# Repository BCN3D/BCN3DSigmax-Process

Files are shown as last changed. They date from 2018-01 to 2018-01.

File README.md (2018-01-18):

# Process Engineering

---

## What’s hold in this repository?
In the present repository you will find all the documentation needed to assemble a BCN3D Sigmax, from the warehouse to the box. In our commitment to Open Source, we want to be transparent, not only in the design, but also in the processes involved in the BCN3D Sigmax manufacture.

Since it’s our first experience producing in an assembly line, we’ve built the structure from the ground up. In the process we have made some mistakes and faced many challenges. But day after day, we improved and deployed a solid system that is allowing us to increase month after month our production capacity in order to satisfy the growing demand.

Read the full story about the Process Engineering performed at the BCN3D facilities at the [BCN3DSigma-Process repository](https://github.com/BCN3D/BCN3DSigma-Process).

After thousands of Sigma units assembled, the process of assembling 3D printers at our facilities has been optimized and the overall quality of the process has been improved. However, it is necessary to keep on fighting and dealing with unexpected problems. In order to minimise the impact of external elements while ensuring the highest quality outcome, BCN3D operators use several guides, jigs, fixtures and technical documentation. All these files can be checked in this repository.

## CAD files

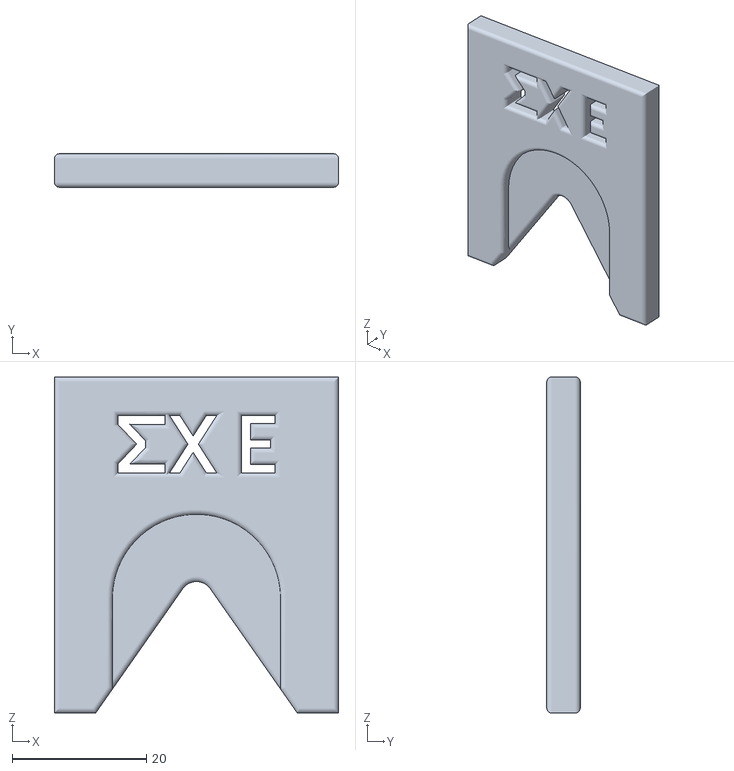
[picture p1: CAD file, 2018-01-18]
Assembly jigs/Separador Drive Gear.STL
42.3 x 5.00 x 50.0

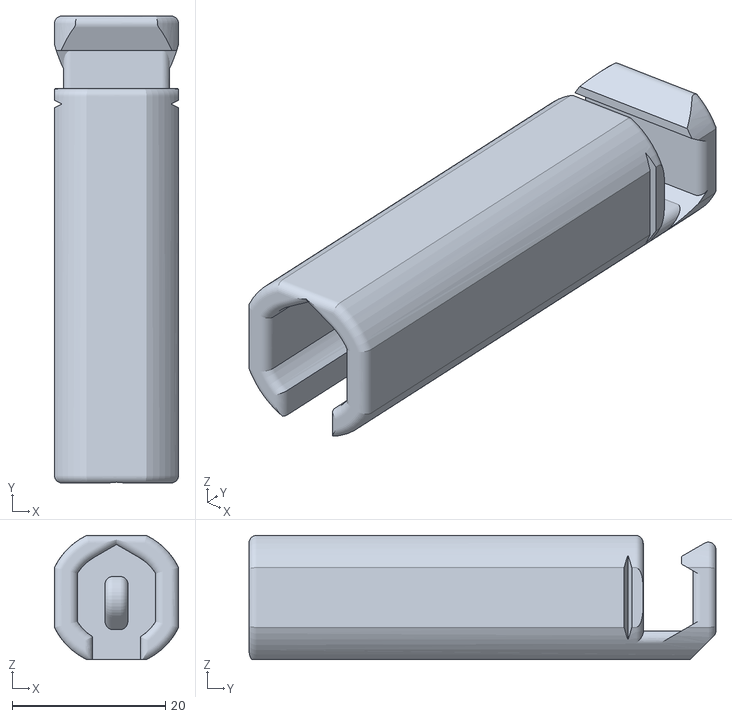
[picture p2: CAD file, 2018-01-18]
Assembly jigs/Hook tensor belt.STL
16.2 x 61.0 x 16.2

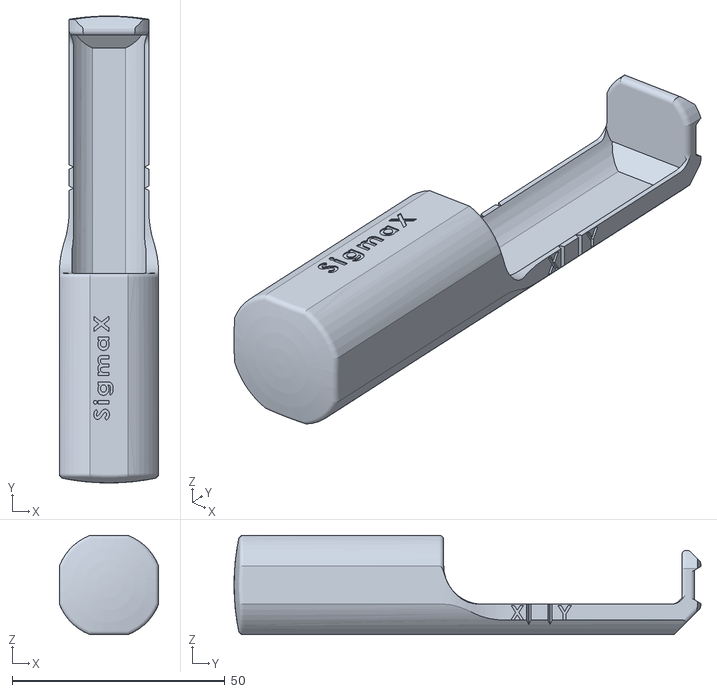
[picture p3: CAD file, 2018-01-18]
Assembly jigs/Body tensor.STL
23.3 x 109.8 x 23.3

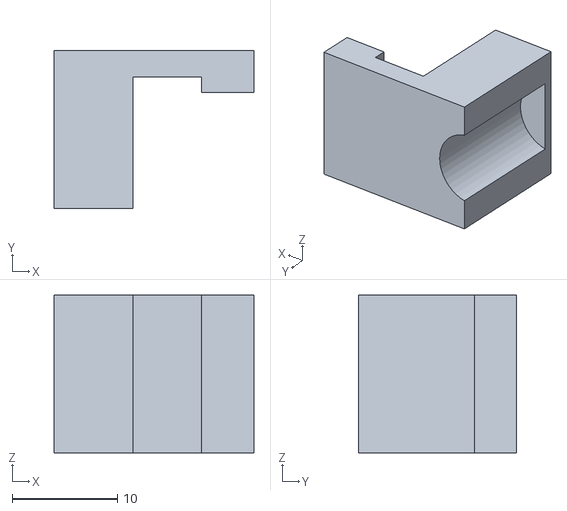
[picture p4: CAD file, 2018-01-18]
Assembly jigs/suport casquillo per talador.STL
19.0 x 15.0 x 15.0

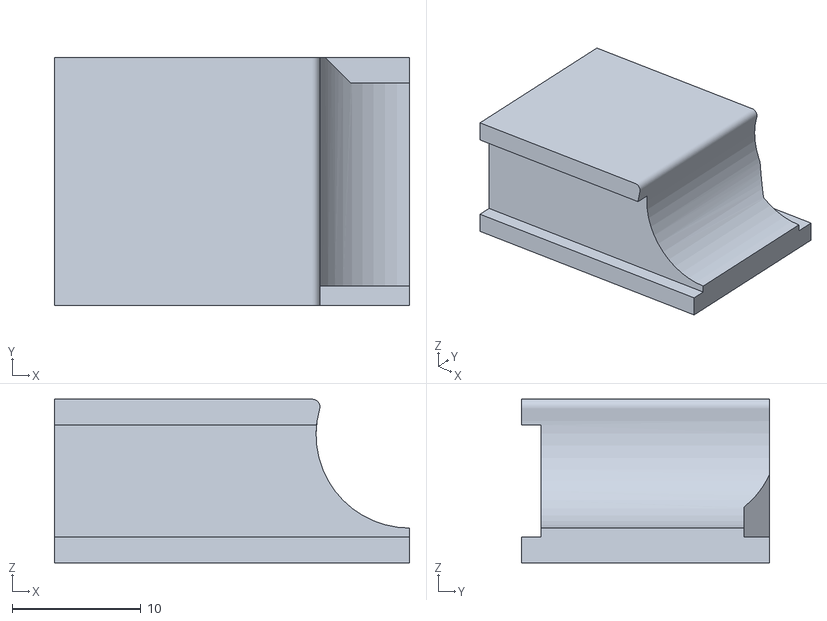
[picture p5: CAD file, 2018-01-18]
Assembly jigs/Util insert Shaft.STL
27.5 x 19.2 x 12.7

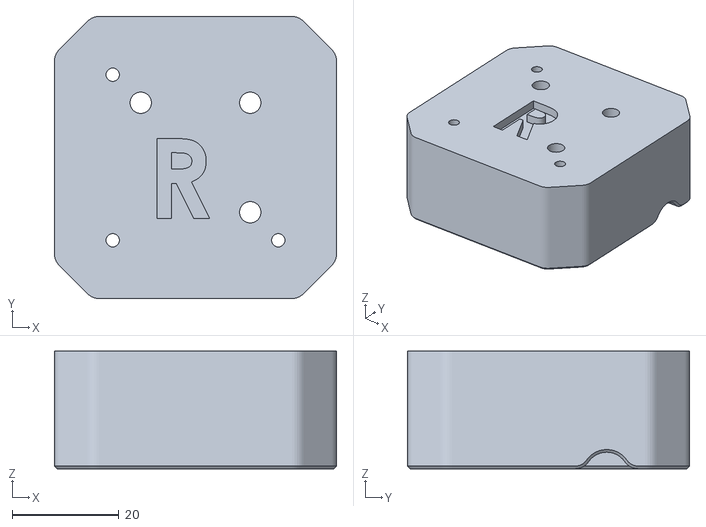
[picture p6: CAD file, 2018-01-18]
Assembly jigs/Fixtures - Right.STL
52.8 x 52.8 x 22.0

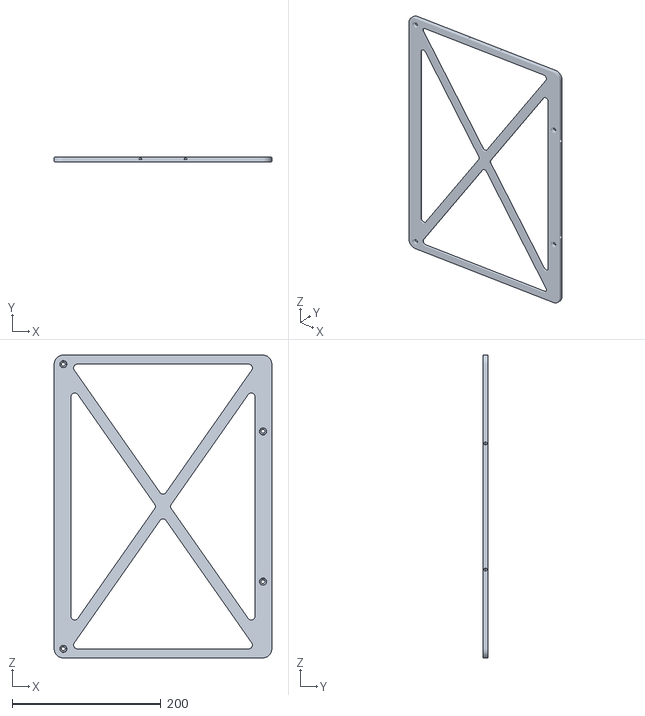
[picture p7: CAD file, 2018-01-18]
Assembly jigs/Útil per posicionar imans - PLASigmaX_v1.2.STL
293.0 x 6.50 x 407.8

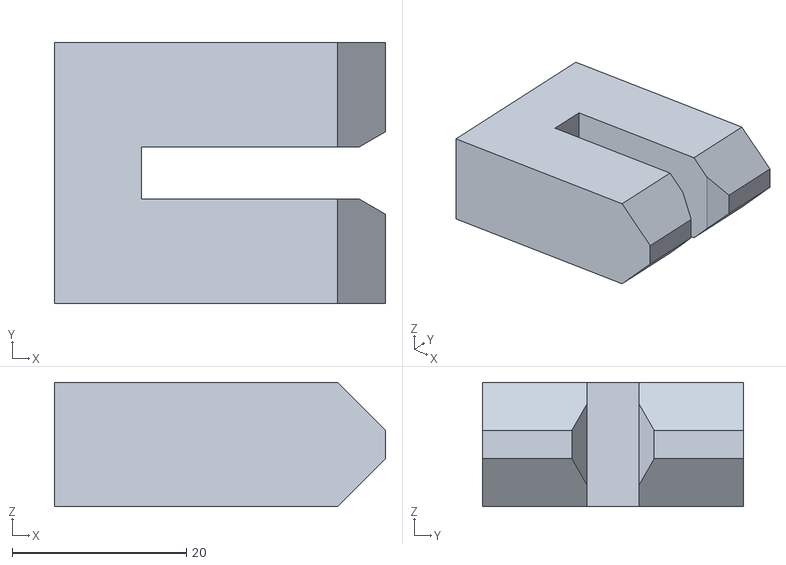
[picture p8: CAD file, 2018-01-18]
Assembly jigs/Util insert anelles.STL
38.0 x 30.0 x 14.3

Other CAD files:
Assembly jigs/Fixtures - Left.STL

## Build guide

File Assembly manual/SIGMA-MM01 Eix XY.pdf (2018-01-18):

## MANUAL DE MUNTATGE

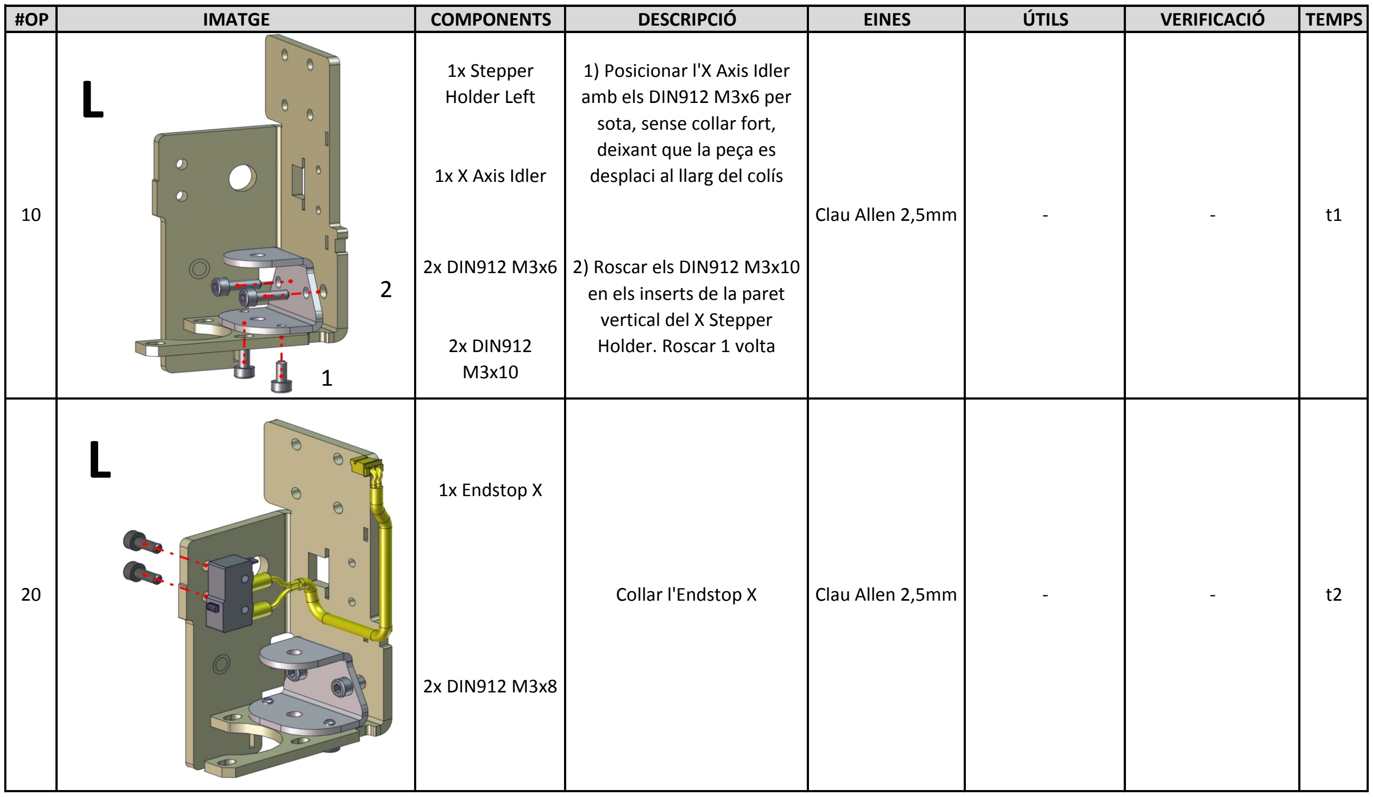
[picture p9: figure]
1x Endstop X; Clau Allen 2,5mm; 2x DIN912 M3x8; 2) Roscar els DIN912 M3x10 en els inserts de la paret vertical del X Stepper Holder. Roscar 1 volta; 1) Posicionar l'X Axis Idler amb els DIN912 M3x6 per sota, sense collar fort, deixant que la peça es desplaci al llarg del colís; Collar l'Endstop X; 2x DIN912 M3x10; 2x DIN912 M3x6; 1x X Axis Idler; 1x Stepper Holder Left L

#OP | IMATGE | COMPONENTS | DESCRIPCIÓ | EINES | ÚTILS | VERIFICACIÓ | TEMPS

CONJUNT | Eix XY
CODI DOCUMENT | SIGMA-MM01 | OPERARIS | 1 | DATA DOCUMENT | 18/01/2018
VERSIÓ DOCUMENT | v04 | TEMPS | T | CONTACTE | E. Pallarés

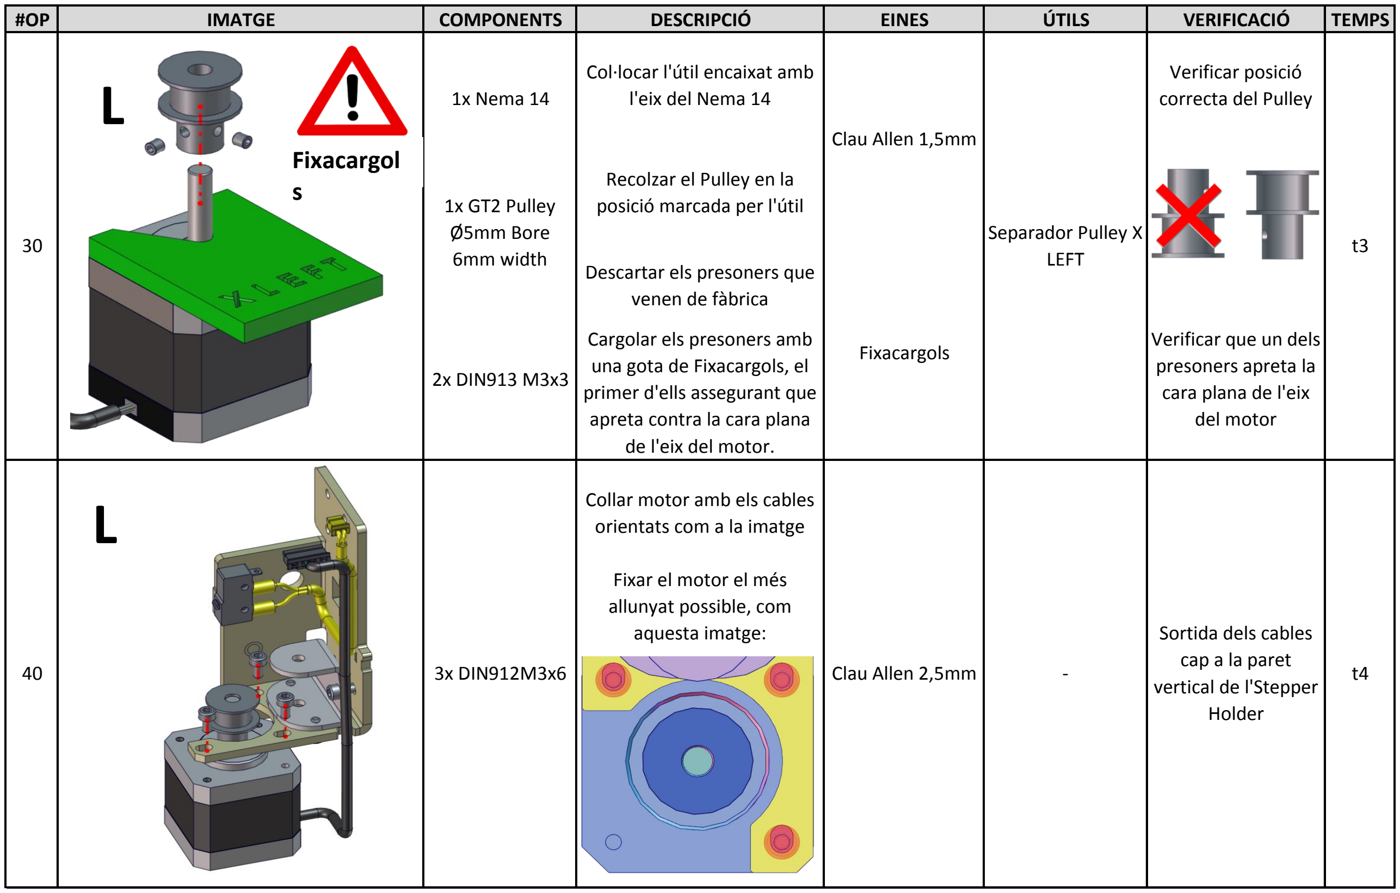
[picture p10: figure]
Cargolar els presoners amb una gota de Fixacargols, el primer d'ells assegurant que apreta contra la cara plana de l'eix del motor.; Clau Allen 1,5mm; Fixacargols; Fixar el motor el més allunyat possible, com aquesta imatge:; Col·locar l'útil encaixat amb l'eix del Nema 14; Recolzar el Pulley en la posició marcada per l'útil; Descartar els presoners que venen de fàbrica; Clau Allen 2,5mm; Sortida dels cables cap a la paret vertical de l'Stepper Holder; 3x DIN912M3x6; Verificar posició correcta del Pulley; Verificar que un dels presoners apreta la cara plana de l'eix del motor; Separador Pulley X LEFT; 1x Nema 14; 1x GT2 Pulley Ø5mm Bore 6mm width; 2x DIN913 M3x3; Collar motor amb els cables orientats com a la imatge; Fixacargol s

#OP | IMATGE | COMPONENTS | DESCRIPCIÓ | EINES | ÚTILS | VERIFICACIÓ | TEMPS

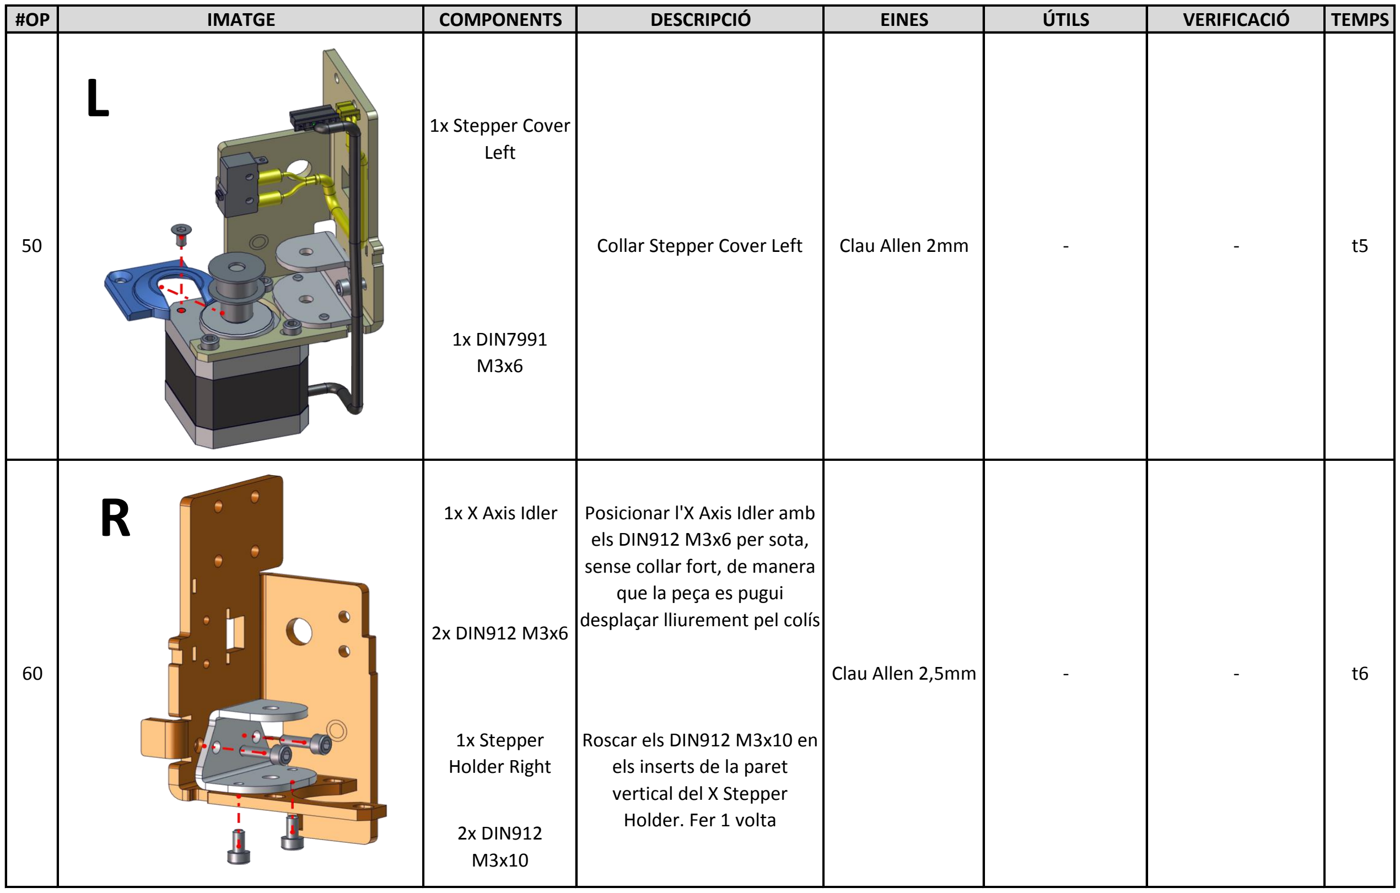
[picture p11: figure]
1x X Axis Idler; 2x DIN912 M3x6; 2x DIN912 M3x10; 1x Stepper Holder Right; Clau Allen 2mm; 1x DIN7991 M3x6; Clau Allen 2,5mm; Roscar els DIN912 M3x10 en els inserts de la paret vertical del X Stepper Holder. Fer 1 volta; Collar Stepper Cover Left; 1x Stepper Cover Left; Posicionar l'X Axis Idler amb els DIN912 M3x6 per sota, sense collar fort, de manera que la peça es pugui desplaçar lliurement pel colís

#OP | IMATGE | COMPONENTS | DESCRIPCIÓ | EINES | ÚTILS | VERIFICACIÓ | TEMPS

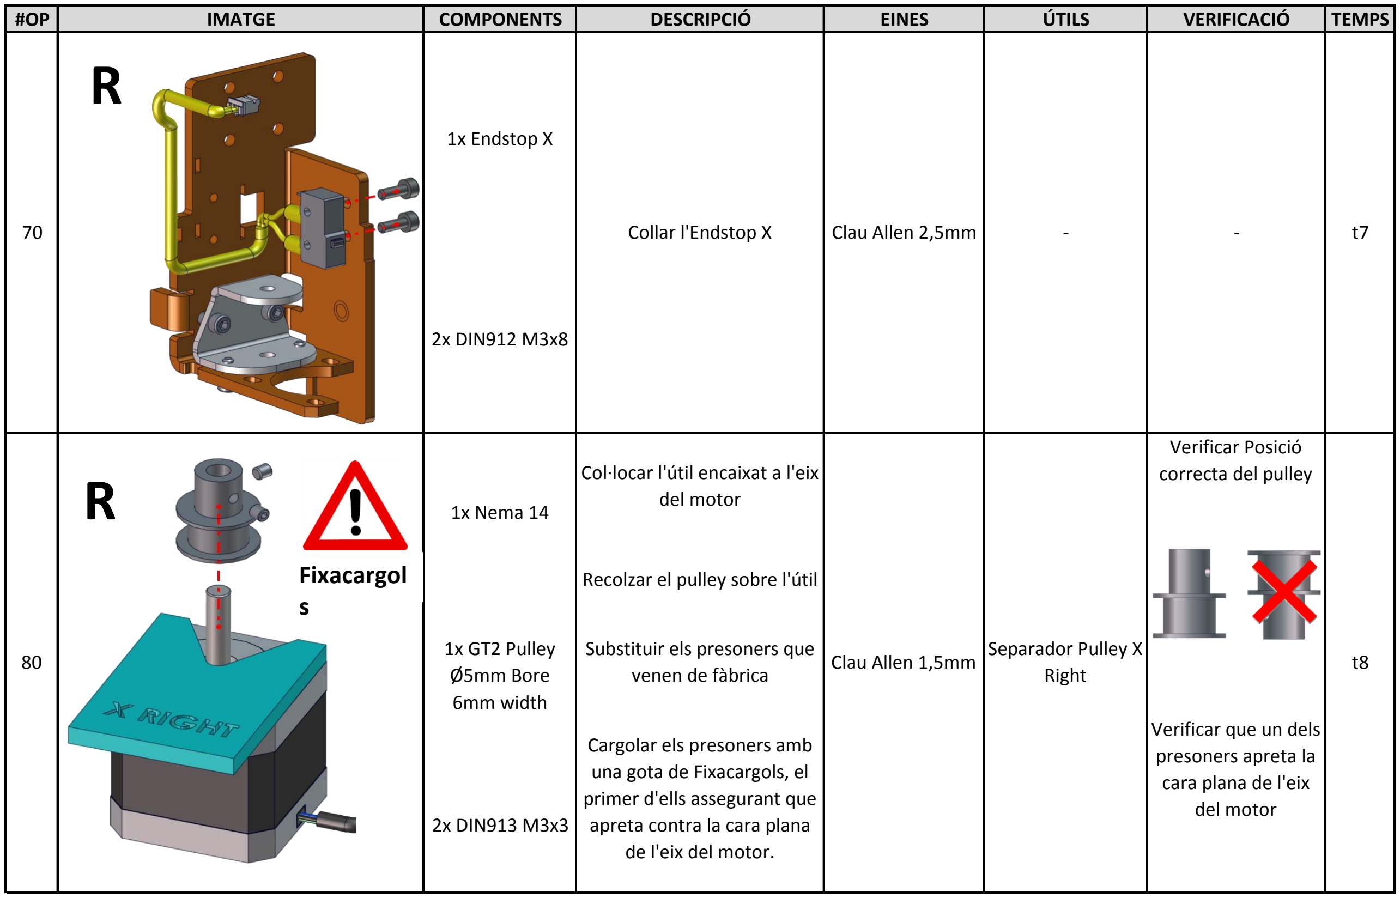
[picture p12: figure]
2x DIN912 M3x8; 1x Endstop X; Substituir els presoners que venen de fàbrica; Cargolar els presoners amb una gota de Fixacargols, el primer d'ells assegurant que apreta contra la cara plana de l'eix del motor.; Col·locar l'útil encaixat a l'eix del motor; Recolzar el pulley sobre l'útil; Verificar que un dels presoners apreta la cara plana de l'eix del motor; Clau Allen 1,5mm; Separador Pulley X; Right; 1x Nema 14; 1x GT2 Pulley Ø5mm Bore 6mm width; 2x DIN913 M3x3; Verificar Posició correcta del pulley; Fixacargol s

#OP | IMATGE | COMPONENTS | DESCRIPCIÓ | EINES | ÚTILS | VERIFICACIÓ | TEMPS

70 | Collar l'Endstop X | Clau Allen 2,5mm | - | - | t7

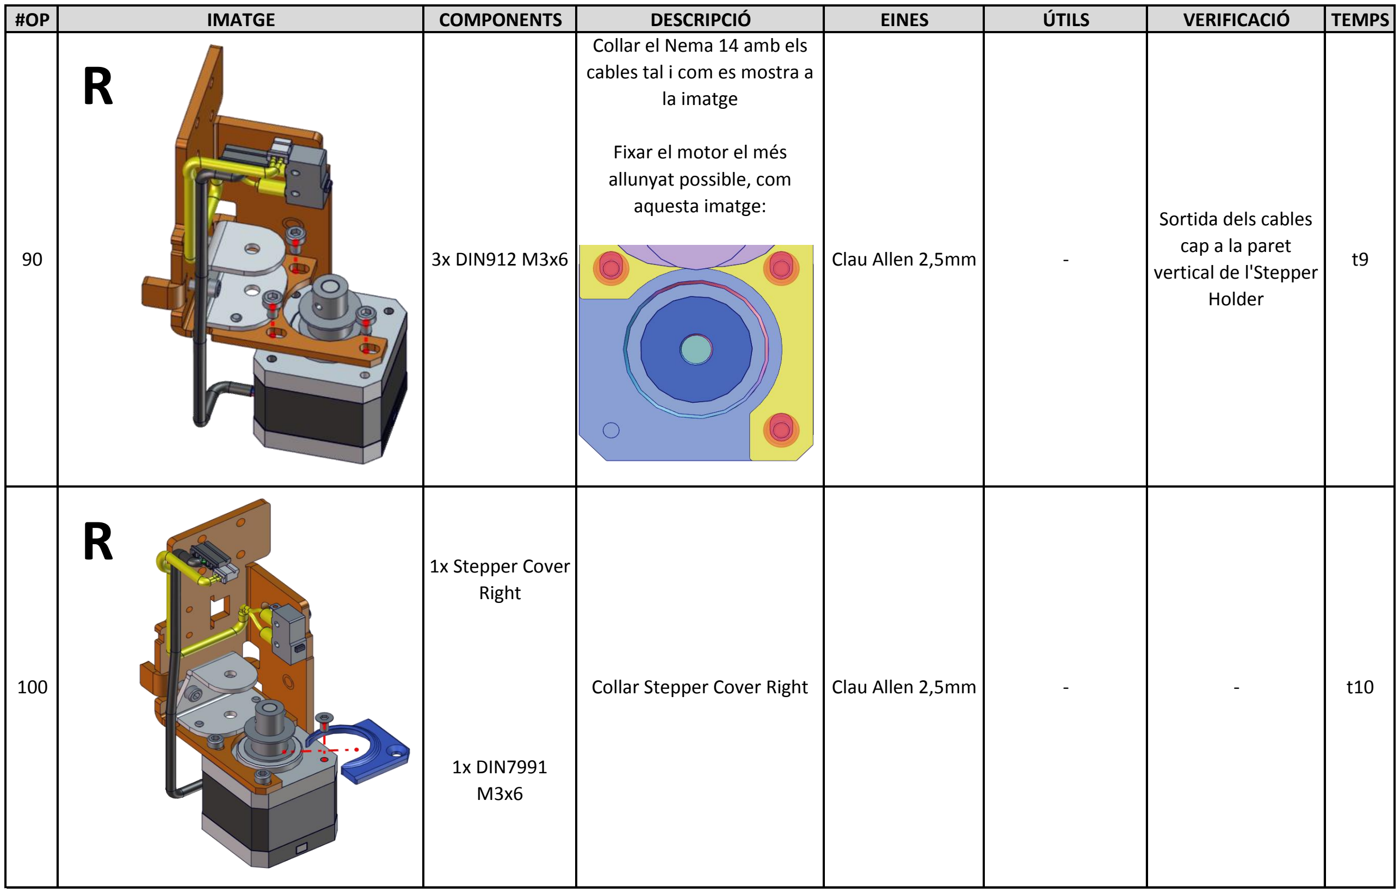
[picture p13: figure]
Fixar el motor el més allunyat possible, com aquesta imatge:; 1x DIN7991 M3x6; Sortida dels cables cap a la paret vertical de l'Stepper Holder; Collar el Nema 14 amb els cables tal i com es mostra a la imatge; 1x Stepper Cover Right; Clau Allen 2,5mm; 3x DIN912 M3x6

#OP | IMATGE | COMPONENTS | DESCRIPCIÓ | EINES | ÚTILS | VERIFICACIÓ | TEMPS

Collar Stepper Cover Right | Clau Allen 2,5mm | -

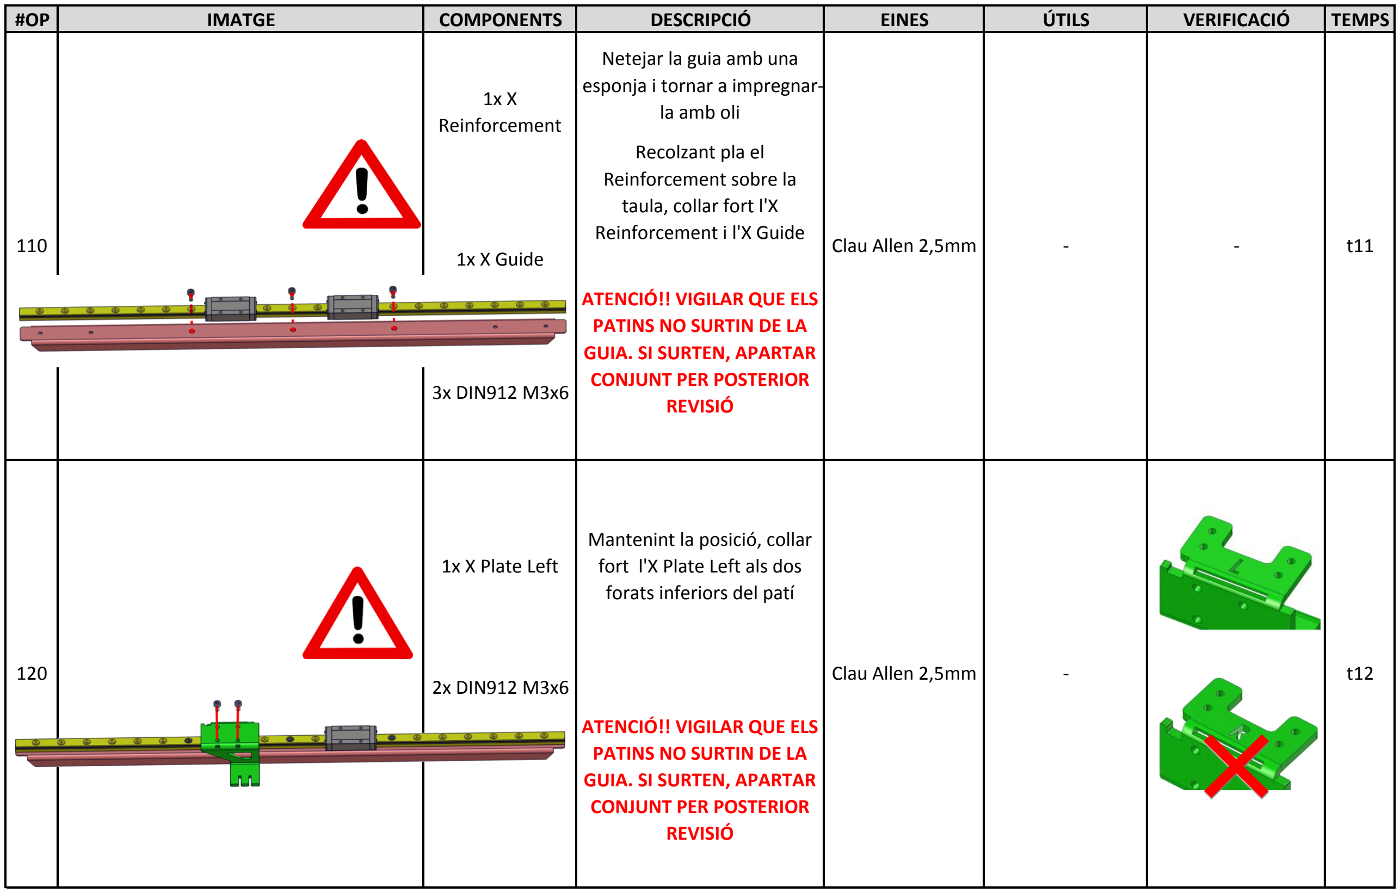
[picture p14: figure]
1x X Reinforcement; 1x X Guide; 3x DIN912 M3x6; Clau Allen 2,5mm; ATENCIÓ!! VIGILAR QUE ELS PATINS NO SURTIN DE LA GUIA. SI SURTEN, APARTAR CONJUNT PER POSTERIOR REVISIÓ; Mantenint la posició, collar fort l'X Plate Left als dos forats inferiors del patí; Recolzant pla el Reinforcement sobre la taula, collar fort l'X Reinforcement i l'X Guide; Netejar la guia amb una esponja i tornar a impregnar- la amb oli; 1x X Plate Left; 2x DIN912 M3x6

#OP | IMATGE | COMPONENTS | DESCRIPCIÓ | EINES | ÚTILS | VERIFICACIÓ | TEMPS

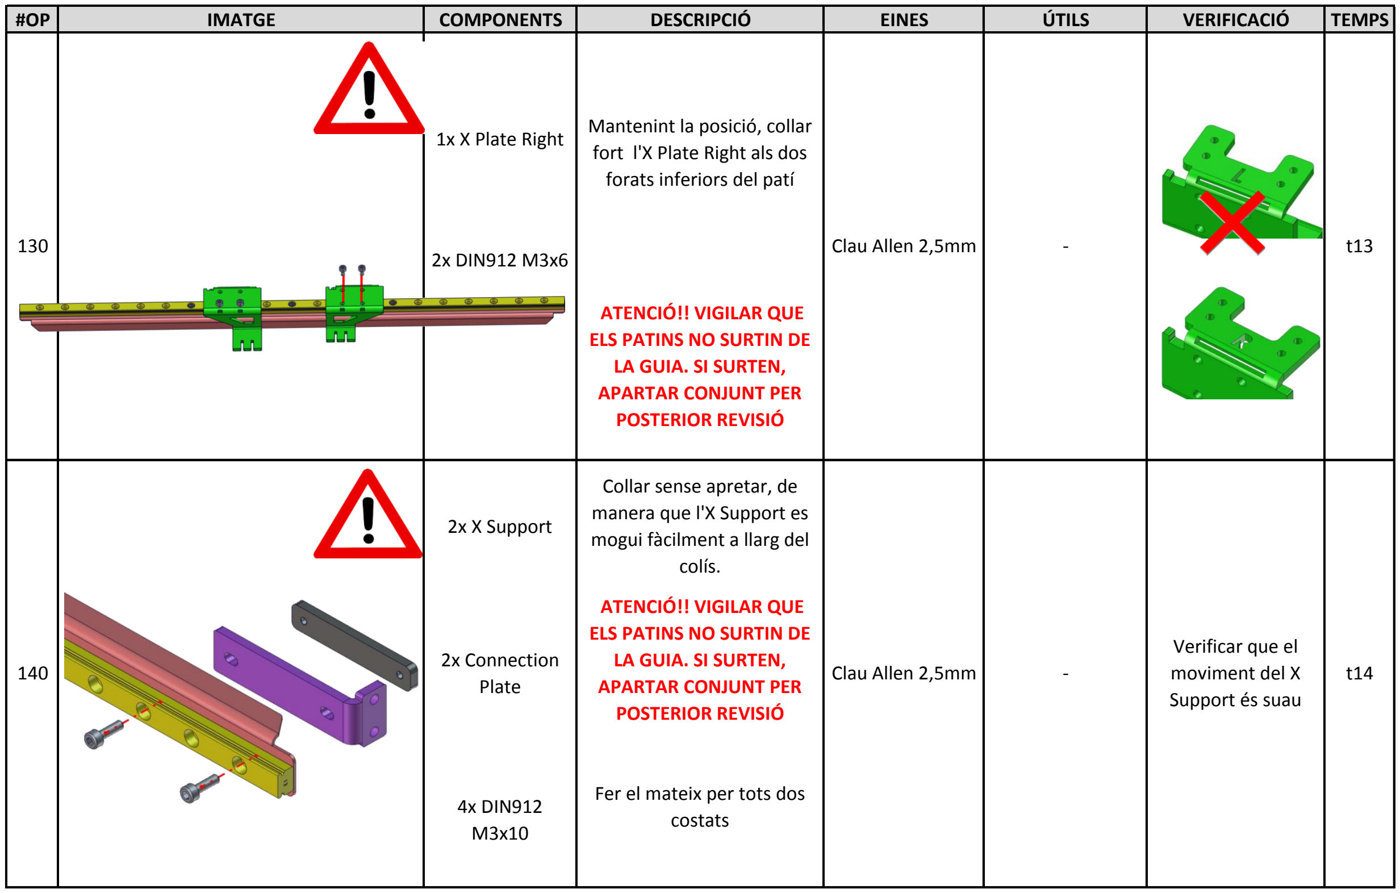
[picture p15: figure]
Fer el mateix per tots dos costats; ATENCIÓ!! VIGILAR QUE ELS PATINS NO SURTIN DE LA GUIA. SI SURTEN, APARTAR CONJUNT PER POSTERIOR REVISIÓ; Collar sense apretar, de manera que l'X Support es mogui fàcilment a llarg del colís.; 2x X Support; 2x Connection Plate; 4x DIN912 M3x10; Clau Allen 2,5mm; Mantenint la posició, collar fort l'X Plate Right als dos forats inferiors del patí; Verificar que el moviment del X Support és suau; 1x X Plate Right; 2x DIN912 M3x6

#OP | IMATGE | COMPONENTS | DESCRIPCIÓ | EINES | ÚTILS | VERIFICACIÓ | TEMPS

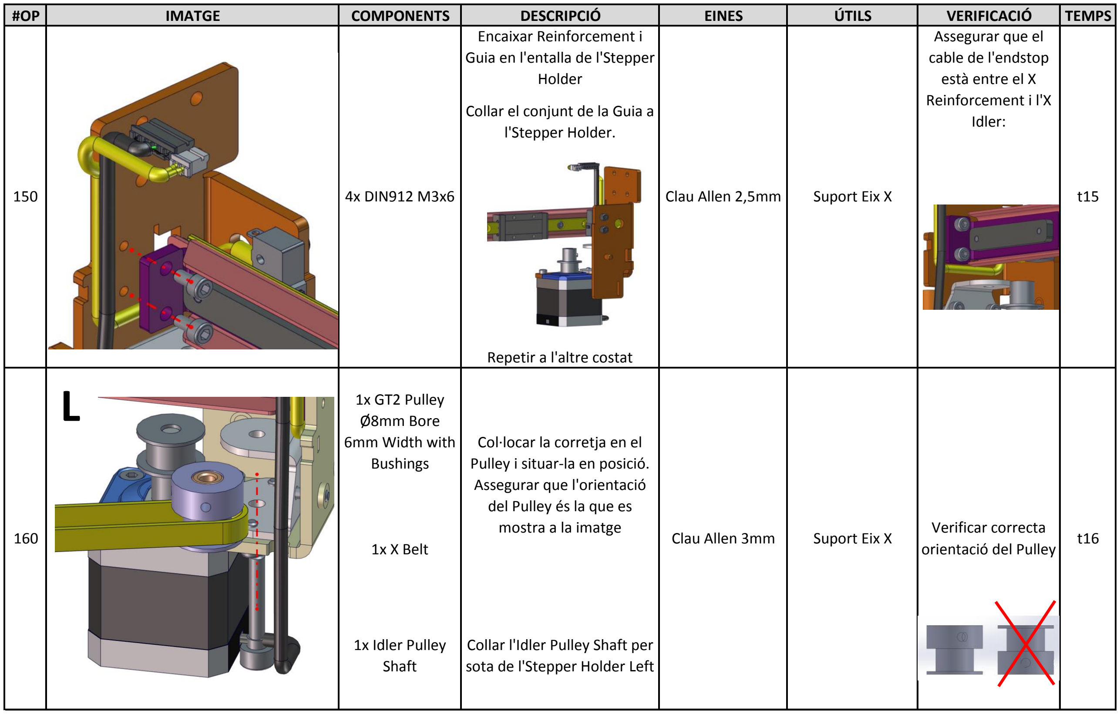
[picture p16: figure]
Repetir a l'altre costat; 1x GT2 Pulley Ø8mm Bore 6mm Width with Bushings; Clau Allen 3mm; Suport Eix X; 4x DIN912 M3x6; Assegurar que el cable de l'endstop està entre el X Reinforcement i l'X Idler:; Clau Allen 2,5mm; 1x X Belt; 1x Idler Pulley Shaft; Collar l'Idler Pulley Shaft per sota de l'Stepper Holder Left; Col·locar la corretja en el Pulley i situar-la en posició. Assegurar que l'orientació del Pulley és la que es mostra a la imatge; Encaixar Reinforcement i Guia en l'entalla de l'Stepper Holder; Collar el conjunt de la Guia a l'Stepper Holder.; Verificar correcta orientació del Pulley

#OP | IMATGE | COMPONENTS | DESCRIPCIÓ | EINES | ÚTILS | VERIFICACIÓ | TEMPS

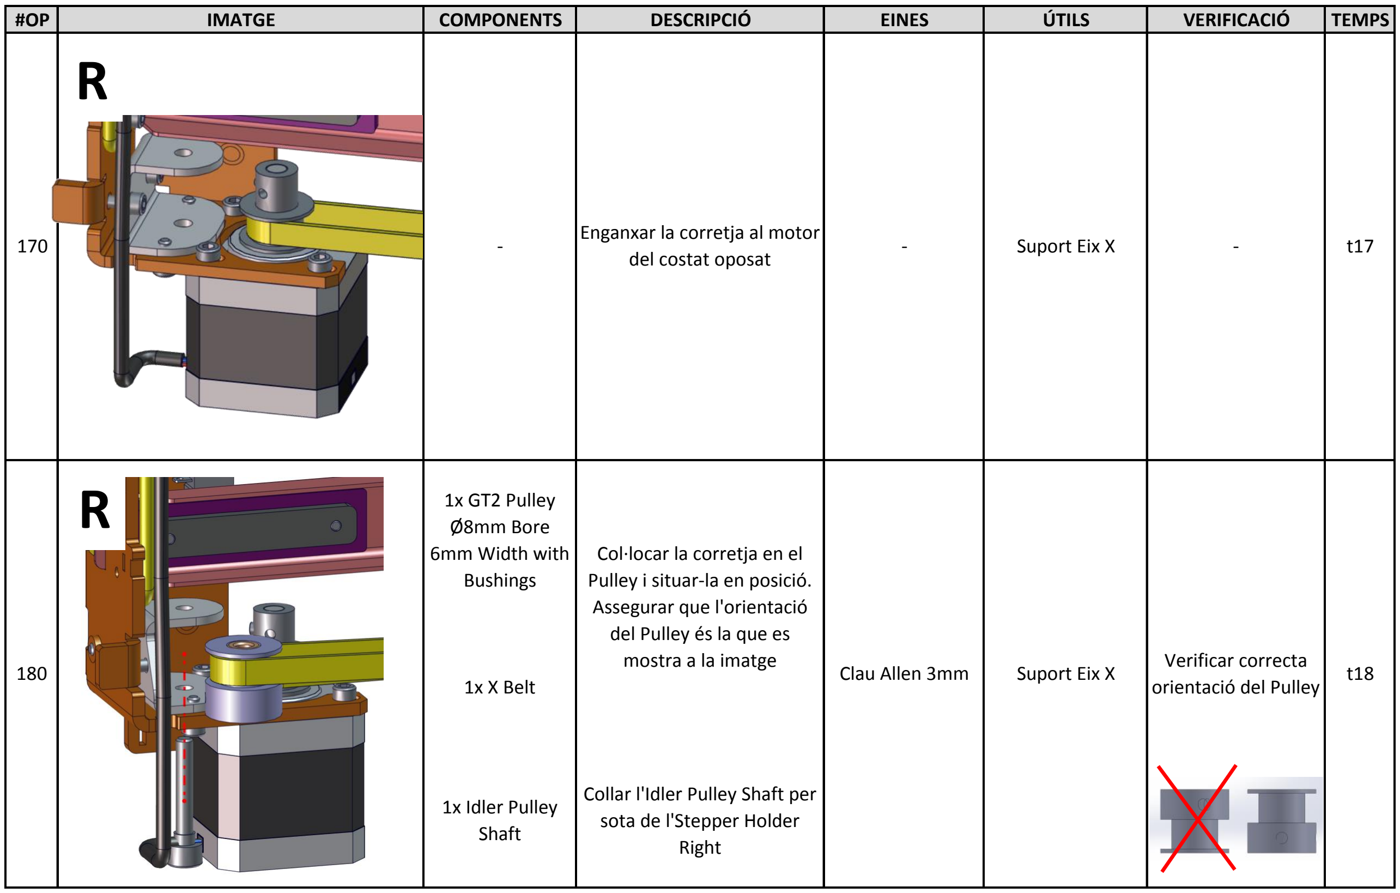
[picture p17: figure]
Enganxar la corretja al motor del costat oposat; 1x GT2 Pulley Ø8mm Bore 6mm Width with Bushings; Col·locar la corretja en el Pulley i situar-la en posició. Assegurar que l'orientació del Pulley és la que es; Verificar correcta; orientació del Pulley; t18 1x X Belt; 1x Idler Pulley Shaft; Collar l'Idler Pulley Shaft per sota de l'Stepper Holder Right; Suport Eix X

#OP | IMATGE | COMPONENTS | DESCRIPCIÓ | EINES | ÚTILS | VERIFICACIÓ | TEMPS

mostra a la imatge | Clau Allen 3mm | Suport Eix X

#OP | IMATGE | COMPONENTS | DESCRIPCIÓ | EINES | ÚTILS | VERIFICACIÓ | TEMPS

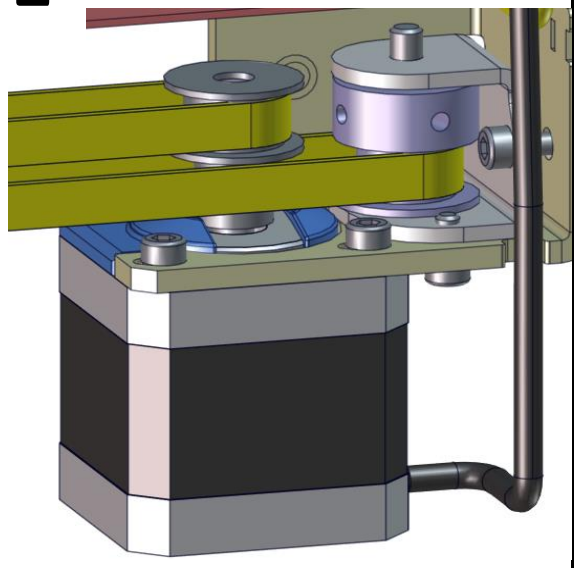
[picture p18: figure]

190 | - | - | Suport Eix X | - | t19

Enganxar la corretja al motor del costat oposat

L

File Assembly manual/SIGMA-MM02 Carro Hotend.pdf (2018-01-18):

## MANUAL DE MUNTATGE

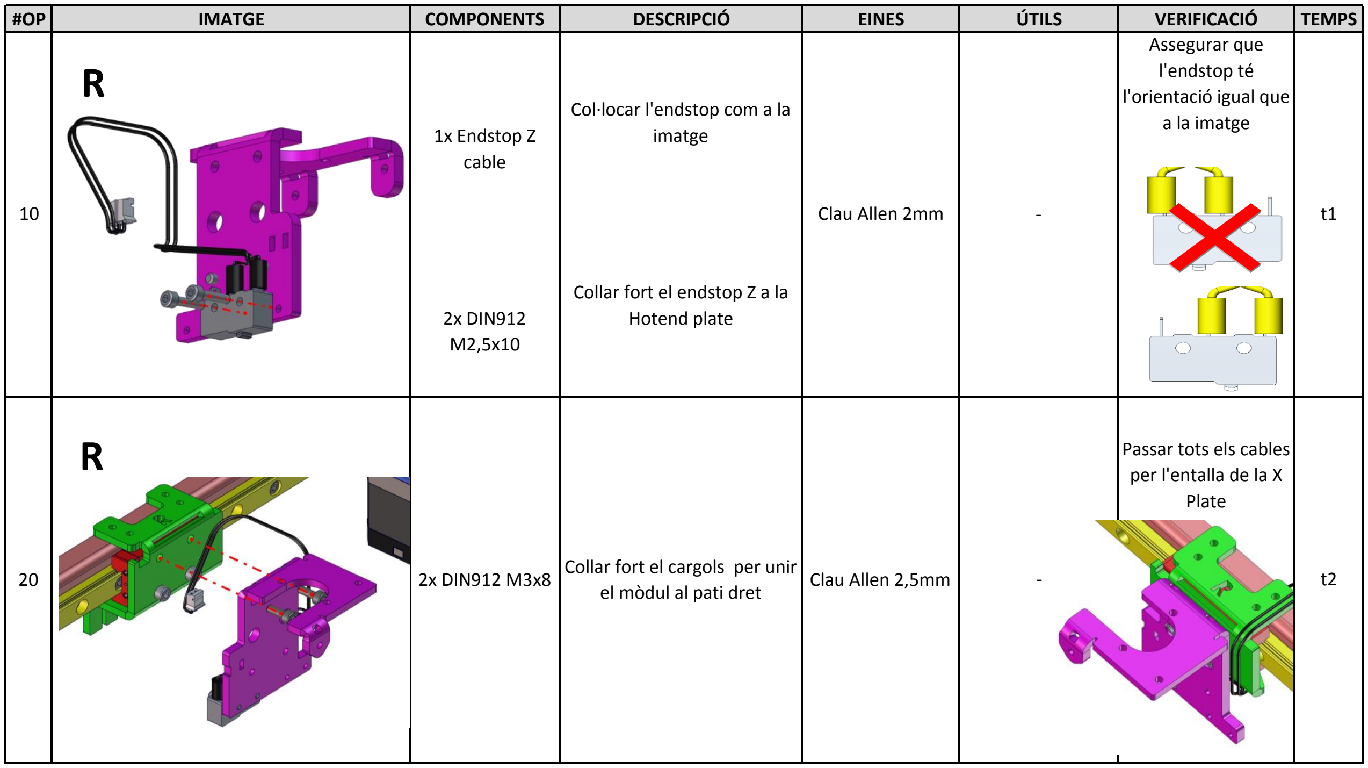
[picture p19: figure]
Collar fort el endstop Z a la; 2x DIN912; Hotend plate; Passar tots els cables per l'entalla de la X Plate; 2x DIN912 M3x8; Collar fort el cargols per unir; el mòdul al pati dret; Clau Allen 2,5mm; 1x Endstop Z cable; Col·locar l'endstop com a la imatge; Clau Allen 2mm; Assegurar que l'endstop té l'orientació igual que a la imatge

#OP | IMATGE | COMPONENTS | DESCRIPCIÓ | EINES | ÚTILS | VERIFICACIÓ | TEMPS

CONJUNT | Carro Hotend
CODI DOCUMENT | SIGMA-MM02 | OPERARIS | 1 | DATA DOCUMENT | 18/01/2018
VERSIÓ DOCUMENT | v04 | TEMPS | T | CONTACTE | E. Pallarés

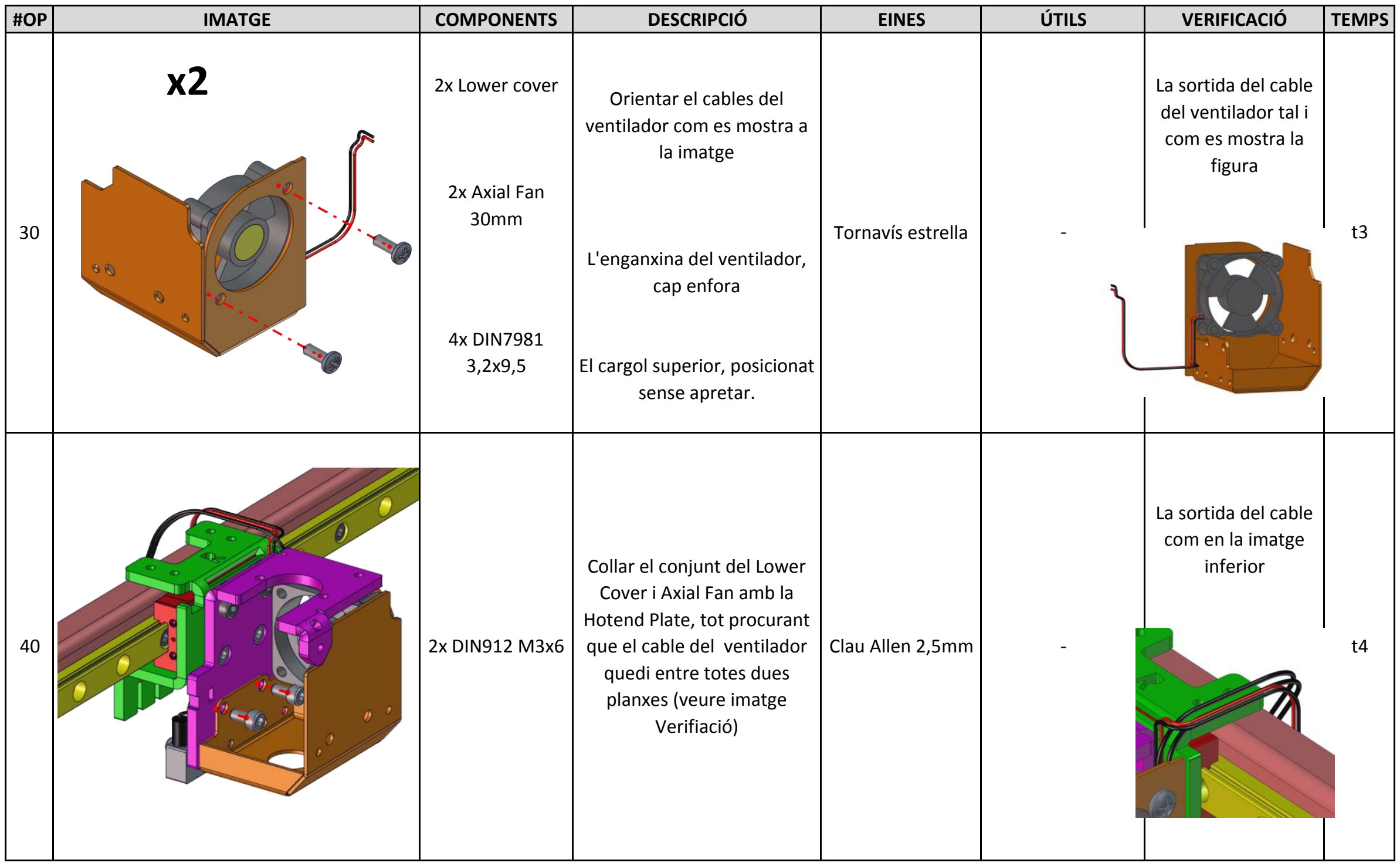
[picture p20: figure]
Orientar el cables del ventilador com es mostra a la imatge; La sortida del cable del ventilador tal i com es mostra la figura; 2x DIN912 M3x6; 2x Lower cover; 2x Axial Fan 30mm; El cargol superior, posicionat sense apretar.; 4x DIN7981 3,2x9,5; Collar el conjunt del Lower Cover i Axial Fan amb la Hotend Plate, tot procurant que el cable del ventilador quedi entre totes dues planxes (veure imatge Verifiació); Tornavís estrella; L'enganxina del ventilador, cap enfora; La sortida del cable com en la imatge inferior; Clau Allen 2,5mm

#OP | IMATGE | COMPONENTS | DESCRIPCIÓ | EINES | ÚTILS | VERIFICACIÓ | TEMPS

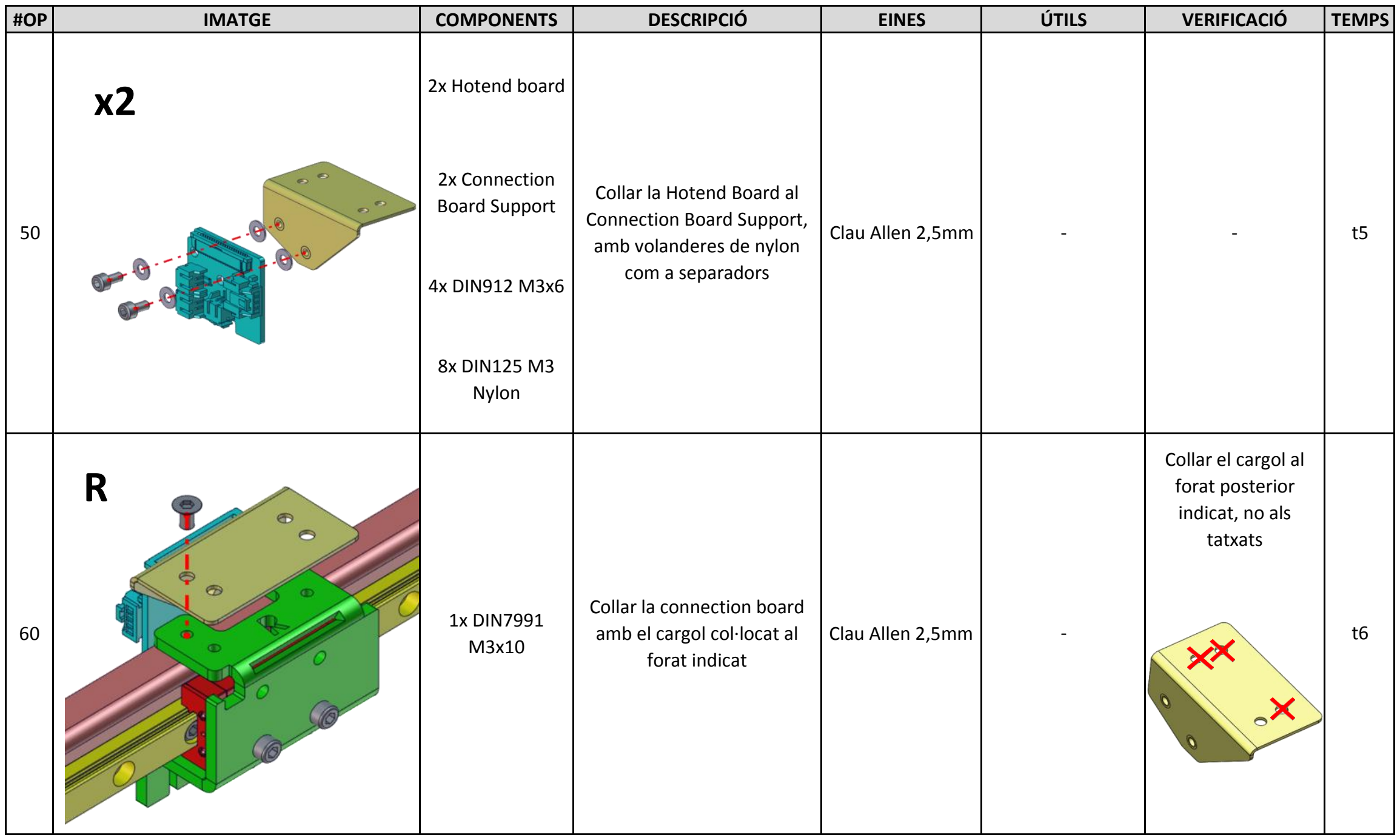
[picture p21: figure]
Clau Allen 2,5mm; Collar la connection board amb el cargol col·locat al forat indicat; 1x DIN7991 M3x10; 4x DIN912 M3x6; 8x DIN125 M3 Nylon; 2x Hotend board; 2x Connection Board Support; Collar el cargol al forat posterior indicat, no als tatxats; Collar la Hotend Board al Connection Board Support, amb volanderes de nylon com a separadors

#OP | IMATGE | COMPONENTS | DESCRIPCIÓ | EINES | ÚTILS | VERIFICACIÓ | TEMPS

#OP | IMATGE | COMPONENTS | DESCRIPCIÓ | EINES | ÚTILS | VERIFICACIÓ | TEMPS

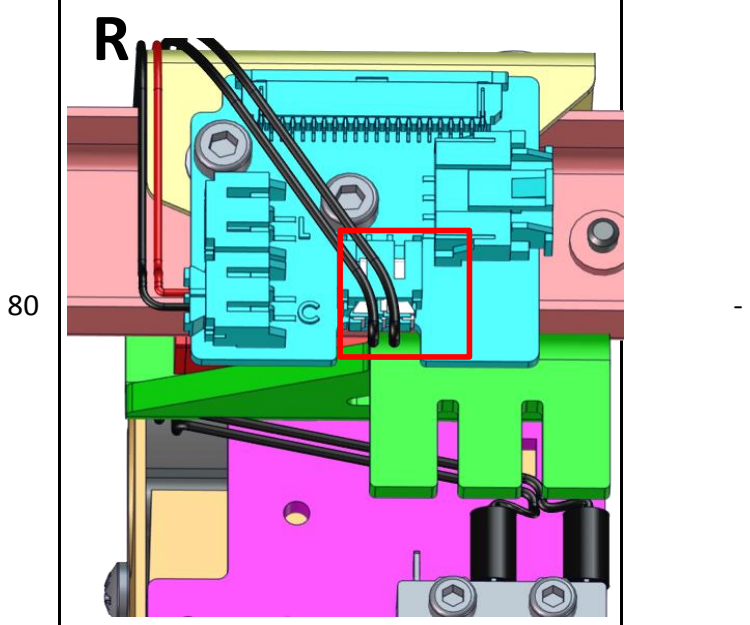
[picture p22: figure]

Connectar l'endstop al
connector indicat | -

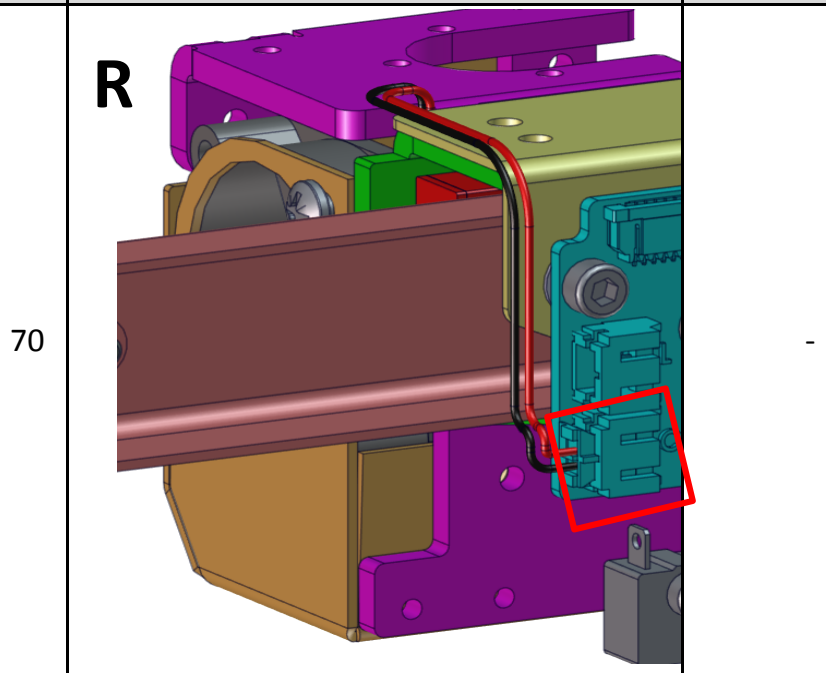
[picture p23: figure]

Trenar els cables i connectar el ventilador del hotend al connector indicat

t7

- | - | t8

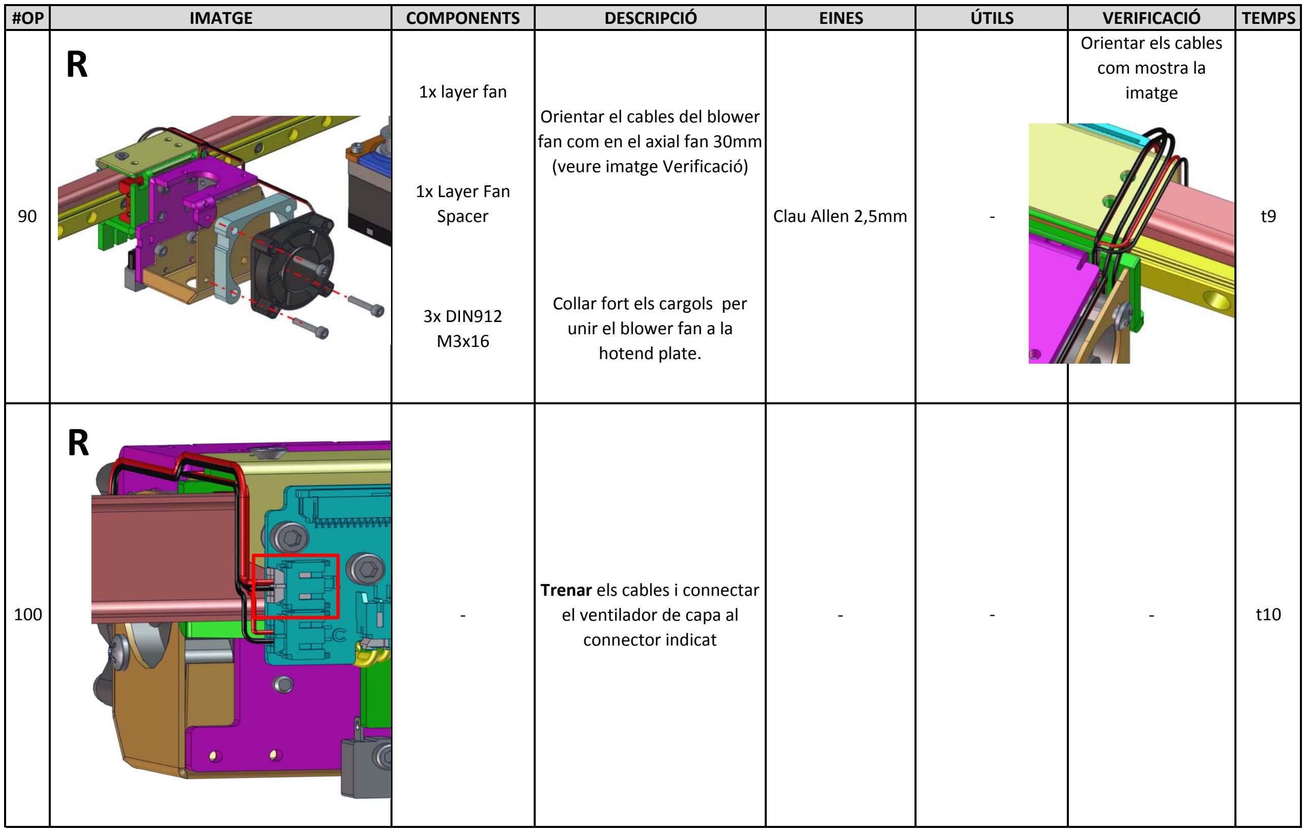
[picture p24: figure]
Trenar els cables i connectar el ventilador de capa al connector indicat; Collar fort els cargols per unir el blower fan a la hotend plate.; Orientar el cables del blower fan com en el axial fan 30mm (veure imatge Verificació); 1x layer fan; 3x DIN912 M3x16; 1x Layer Fan Spacer; Clau Allen 2,5mm; Orientar els cables com mostra la imatge

#OP | IMATGE | COMPONENTS | DESCRIPCIÓ | EINES | ÚTILS | VERIFICACIÓ | TEMPS

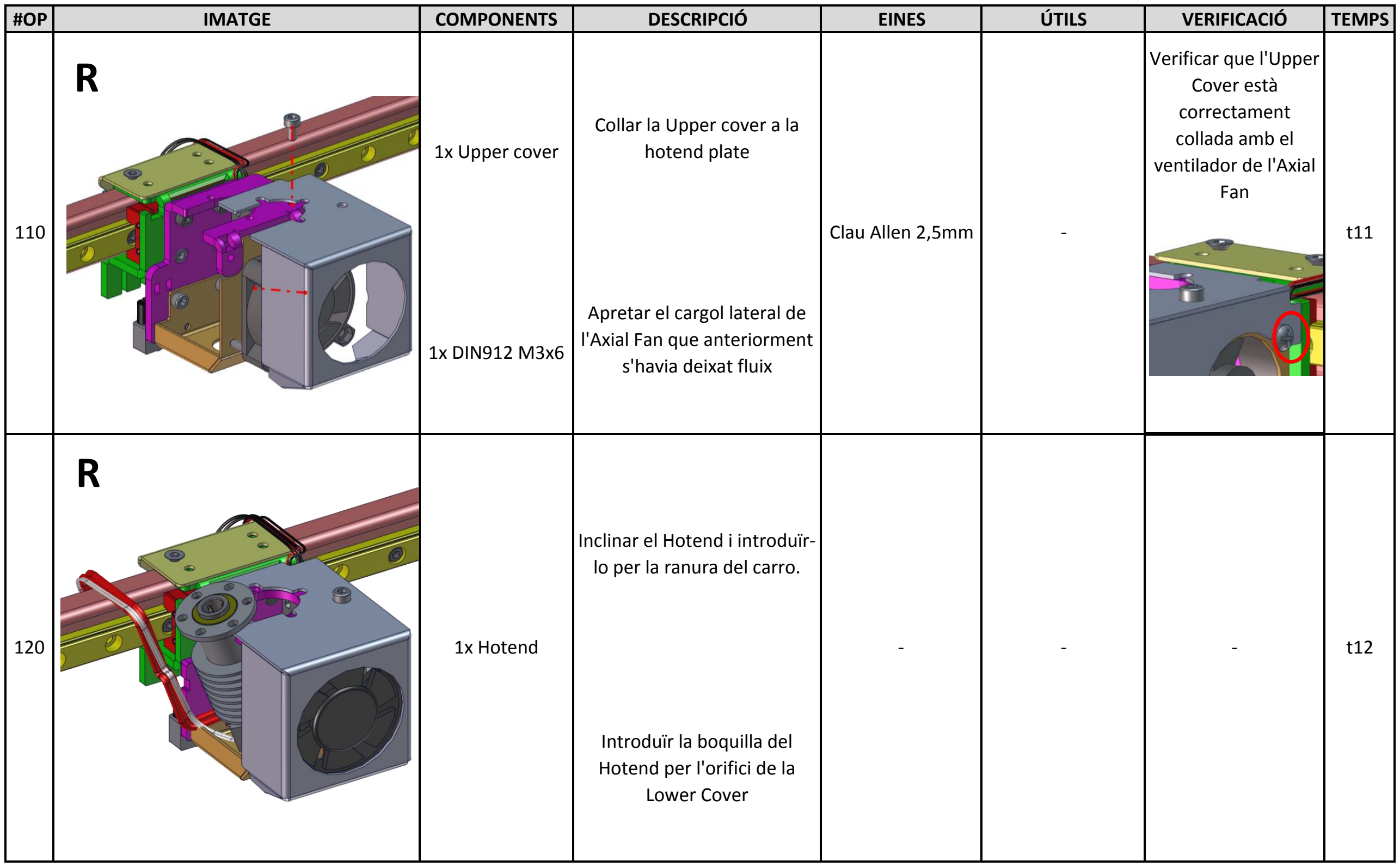
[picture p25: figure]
Inclinar el Hotend i introduïr- lo per la ranura del carro.; 1x Upper cover; Introduïr la boquilla del Hotend per l'orifici de la Lower Cover; 1x Hotend; 1x DIN912 M3x6; Clau Allen 2,5mm; Collar la Upper cover a la hotend plate; Apretar el cargol lateral de l'Axial Fan que anteriorment s'havia deixat fluix; Verificar que l'Upper Cover està correctament collada amb el ventilador de l'Axial Fan

#OP | IMATGE | COMPONENTS | DESCRIPCIÓ | EINES | ÚTILS | VERIFICACIÓ | TEMPS

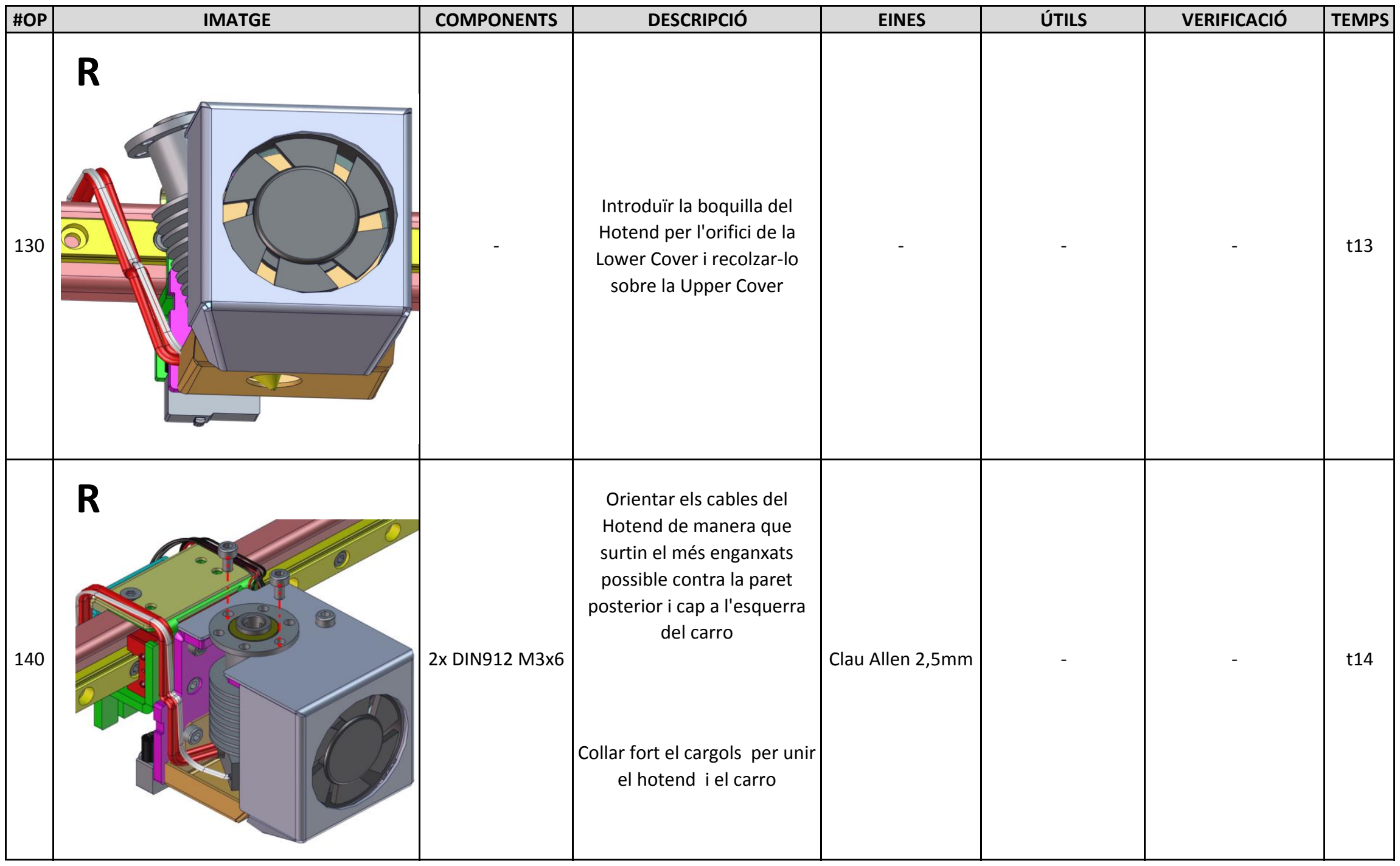
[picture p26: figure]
Orientar els cables del Hotend de manera que surtin el més enganxats possible contra la paret posterior i cap a l'esquerra del carro; Clau Allen 2,5mm; Introduïr la boquilla del Hotend per l'orifici de la Lower Cover i recolzar-lo sobre la Upper Cover; Collar fort el cargols per unir el hotend i el carro; 2x DIN912 M3x6

#OP | IMATGE | COMPONENTS | DESCRIPCIÓ | EINES | ÚTILS | VERIFICACIÓ | TEMPS

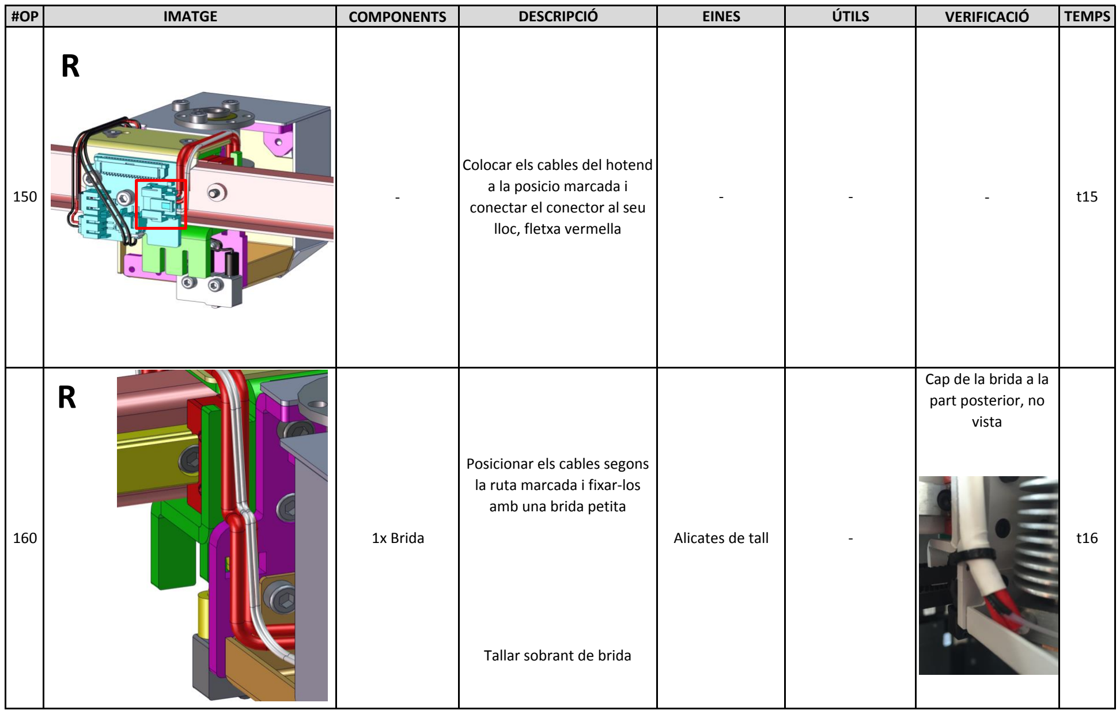
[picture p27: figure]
1x Brida; Alicates de tall; Cap de la brida a la part posterior, no vista; Colocar els cables del hotend a la posicio marcada i conectar el conector al seu lloc, fletxa vermella; Posicionar els cables segons la ruta marcada i fixar-los amb una brida petita; Tallar sobrant de brida

#OP | IMATGE | COMPONENTS | DESCRIPCIÓ | EINES | ÚTILS | VERIFICACIÓ | TEMPS

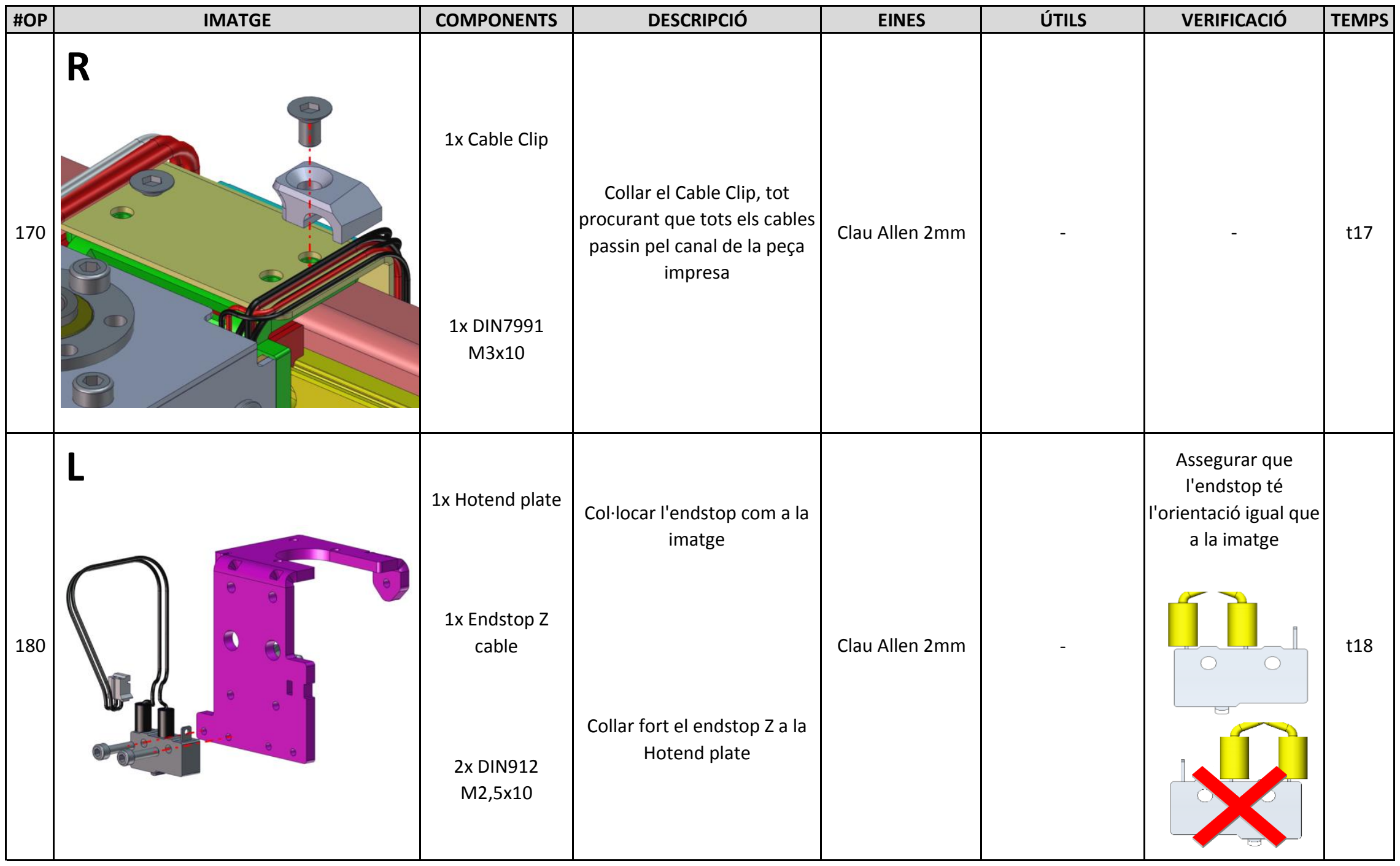
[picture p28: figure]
Collar el Cable Clip, tot procurant que tots els cables passin pel canal de la peça impresa; imatge; Clau Allen 2mm; 1x Cable Clip; 1x DIN7991 M3x10; 1x Endstop Z cable; Collar fort el endstop Z a la Hotend plate; 2x DIN912 M2,5x10; Assegurar que l'endstop té l'orientació igual que a la imatge

#OP | IMATGE | COMPONENTS | DESCRIPCIÓ | EINES | ÚTILS | VERIFICACIÓ | TEMPS

1x Hotend plate | Col·locar l'endstop com a la

#OP | IMATGE | COMPONENTS | DESCRIPCIÓ | EINES | ÚTILS | VERIFICACIÓ | TEMPS

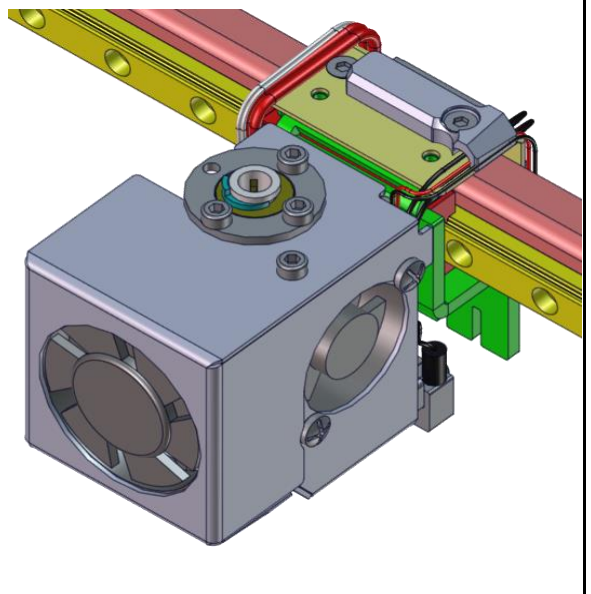
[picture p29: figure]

190 | t19

Acabar muntatge del mòdul
seguint les operacions 10-170

L

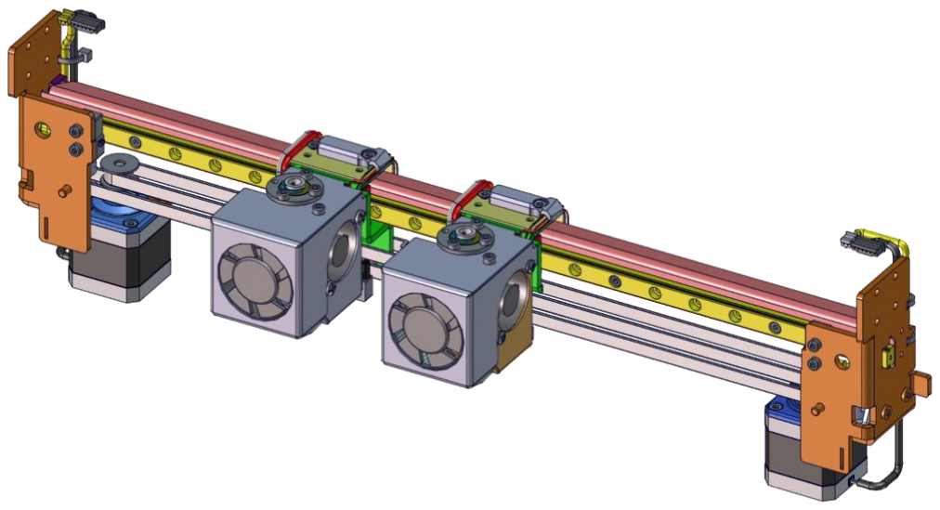
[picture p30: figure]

#OP | IMATGE | COMPONENTS | DESCRIPCIÓ | EINES | ÚTILS | VERIFICACIÓ | TEMPS

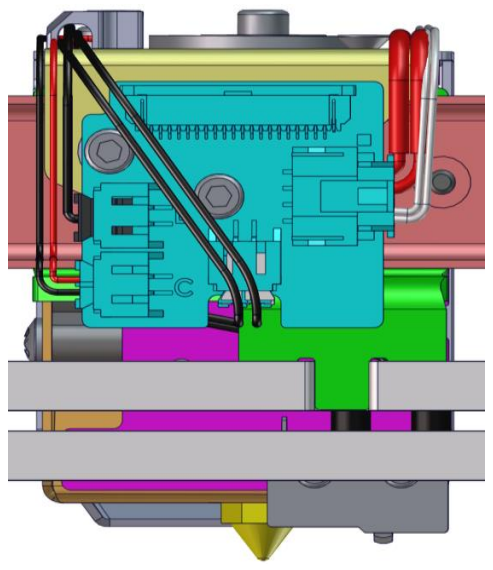
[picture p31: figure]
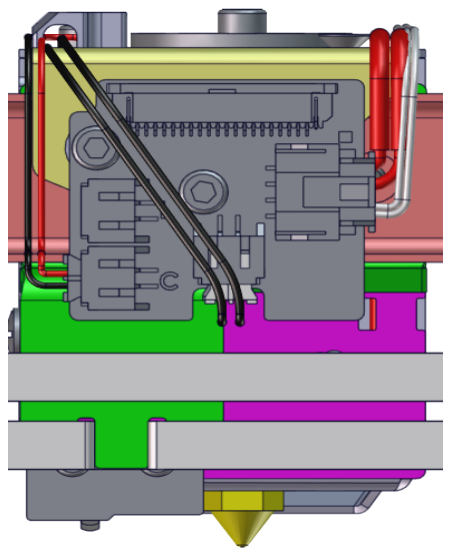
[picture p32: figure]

210 | - | - | - | t21

Enganxar corretja inferior a
capçal de l'esquerra | -

200

Enganxar corretja superior a
capçal de la dreta - | - | - | - | t20

L

R

#OP | IMATGE | COMPONENTS | DESCRIPCIÓ | EINES | ÚTILS | VERIFICACIÓ | TEMPS

Enganxar cables dels laterals de l'eix X amb brides,
procurant que el cap quedi a la paret posterior

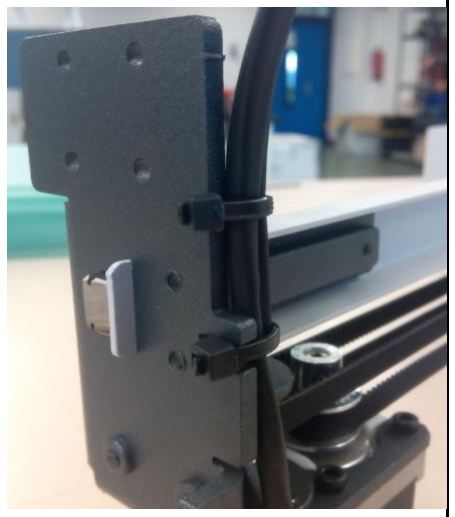
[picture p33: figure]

220 | 4x Brides | Alicates tall | - | - | t22

R

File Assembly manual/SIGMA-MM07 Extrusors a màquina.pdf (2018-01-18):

## MANUAL DE MUNTATGE

#OP | IMATGE | COMPONENTS | DESCRIPCIÓ | EINES | ÚTILS | VERIFICACIÓ | TEMPS

Collar fort el mòdul de

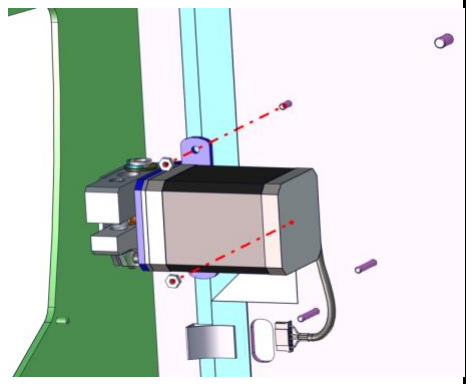
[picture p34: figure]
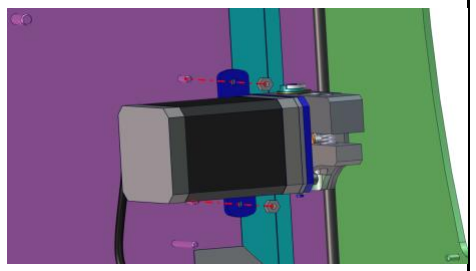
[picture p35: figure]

l'extrusor a l'estructura 20 | 2x DIN934 M3 | Clau tub 5,5mm | - | - | t2
CONJUNT | Extrusors a màquina
CODI DOCUMENT | SIGMA-MM07 | OPERARIS | 1 | DATA DOCUMENT | 18/01/2018
VERSIÓ DOCUMENT | v04 | TEMPS | T | CONTACTE | E. Pallarés
10 | - | t1

Collar fort el mòdul de
l'extrusor a l'estructura 2x DIN934 M3 | Clau tub 5,5mm | -

L

R

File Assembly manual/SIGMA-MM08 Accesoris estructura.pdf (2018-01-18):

## MANUAL DE MUNTATGE

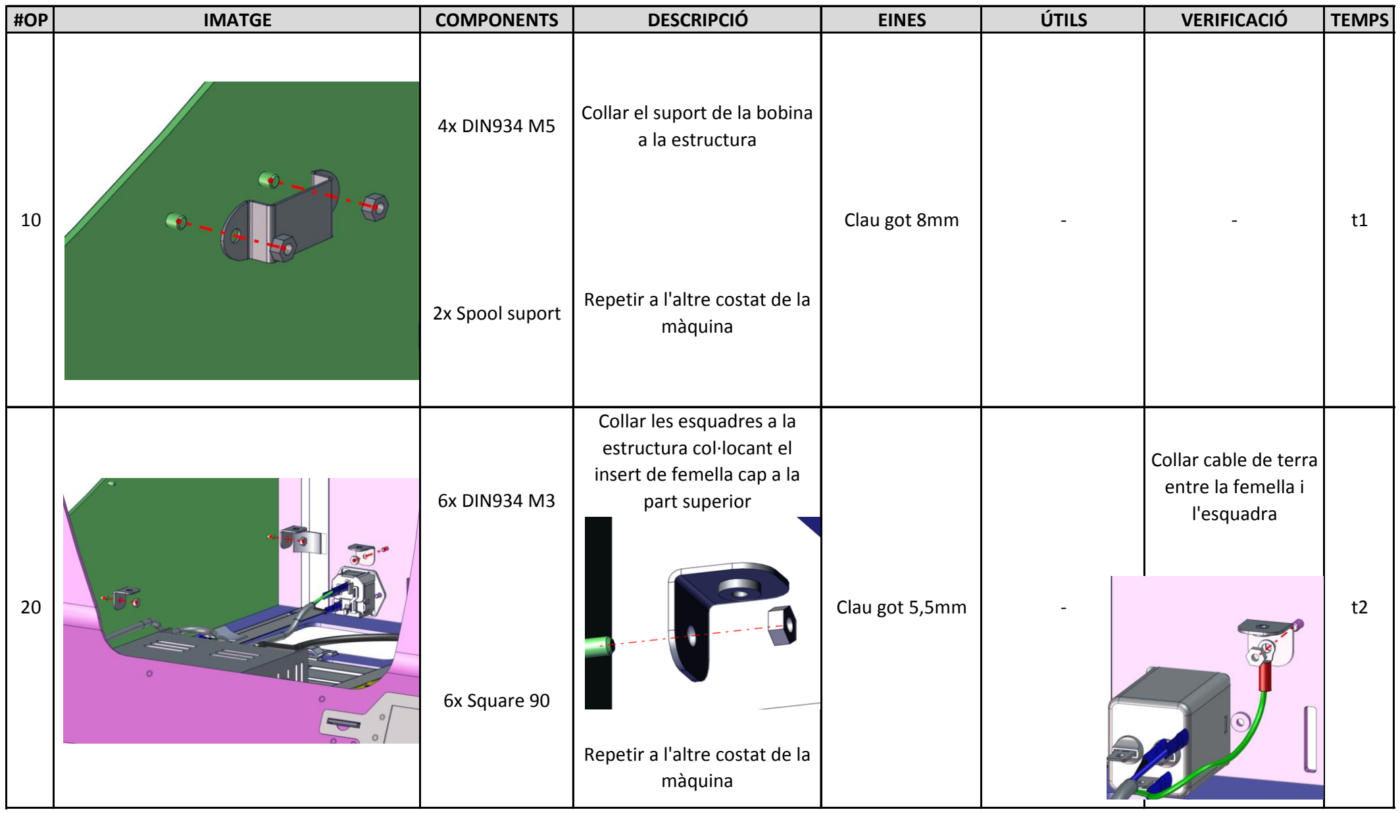
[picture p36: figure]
4x DIN934 M5; 2x Spool suport; Clau got 8mm; Collar les esquadres a la estructura col·locant el insert de femella cap a la part superior; Repetir a l'altre costat de la màquina; 6x DIN934 M3; 6x Square 90; Collar el suport de la bobina a la estructura; Collar cable de terra entre la femella i l'esquadra; Clau got 5,5mm

#OP | IMATGE | COMPONENTS | DESCRIPCIÓ | EINES | ÚTILS | VERIFICACIÓ | TEMPS

CONJUNT | Accessoris Estructura
CODI DOCUMENT | SIGMA-MM08 | DATA DOCUMENT | OPERARIS | 1 | 18/01/2018
VERSIÓ DOCUMENT | v04 | CONTACTE | TEMPS | T | E. Pallarés

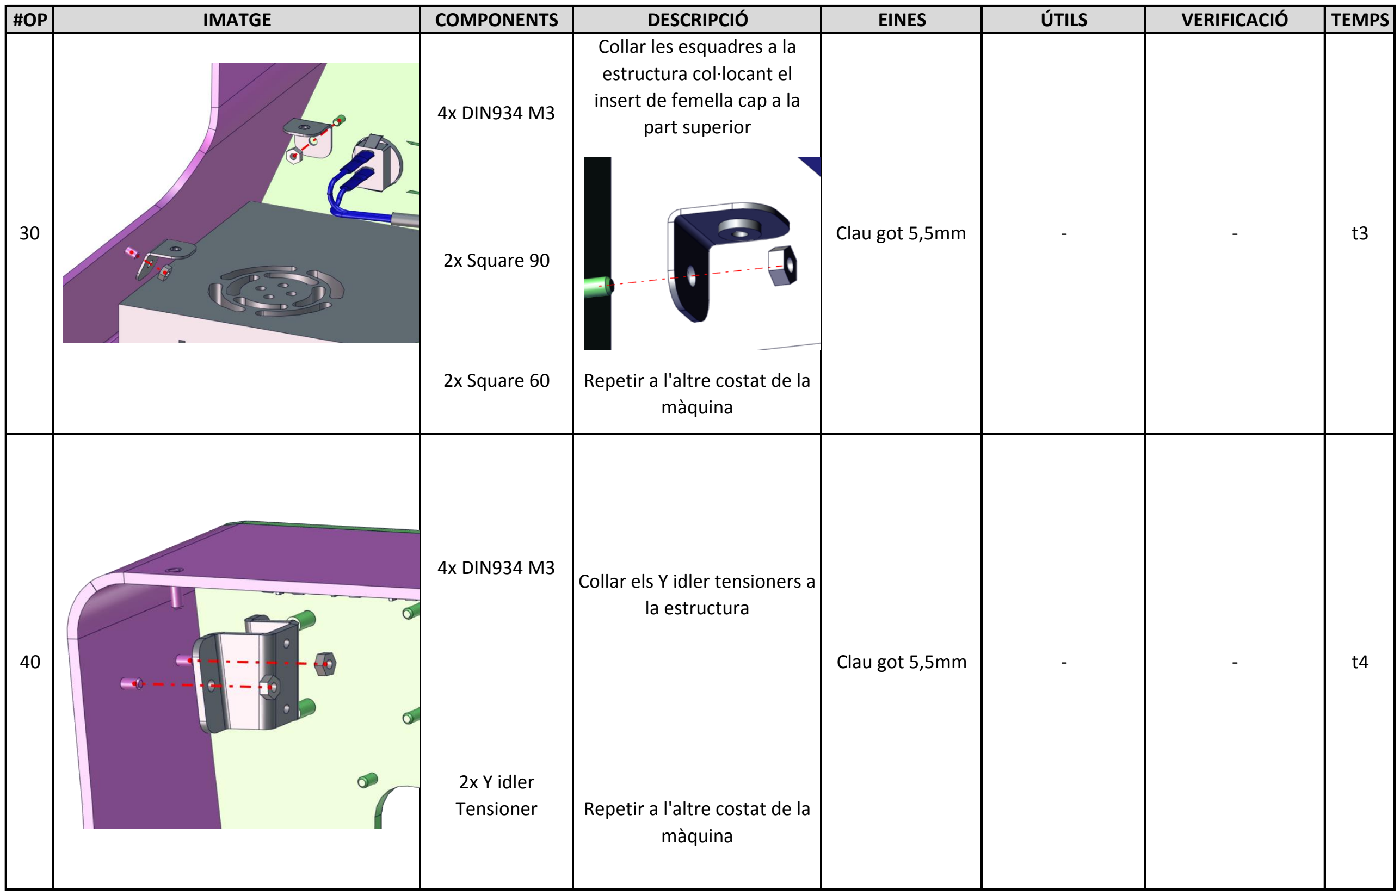
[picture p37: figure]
2x Square 90; 2x Square 60; 4x DIN934 M3; 2x Y idler Tensioner; Repetir a l'altre costat de la màquina; Clau got 5,5mm; Collar les esquadres a la estructura col·locant el insert de femella cap a la part superior; Collar els Y idler tensioners a la estructura

#OP | IMATGE | COMPONENTS | DESCRIPCIÓ | EINES | ÚTILS | VERIFICACIÓ | TEMPS

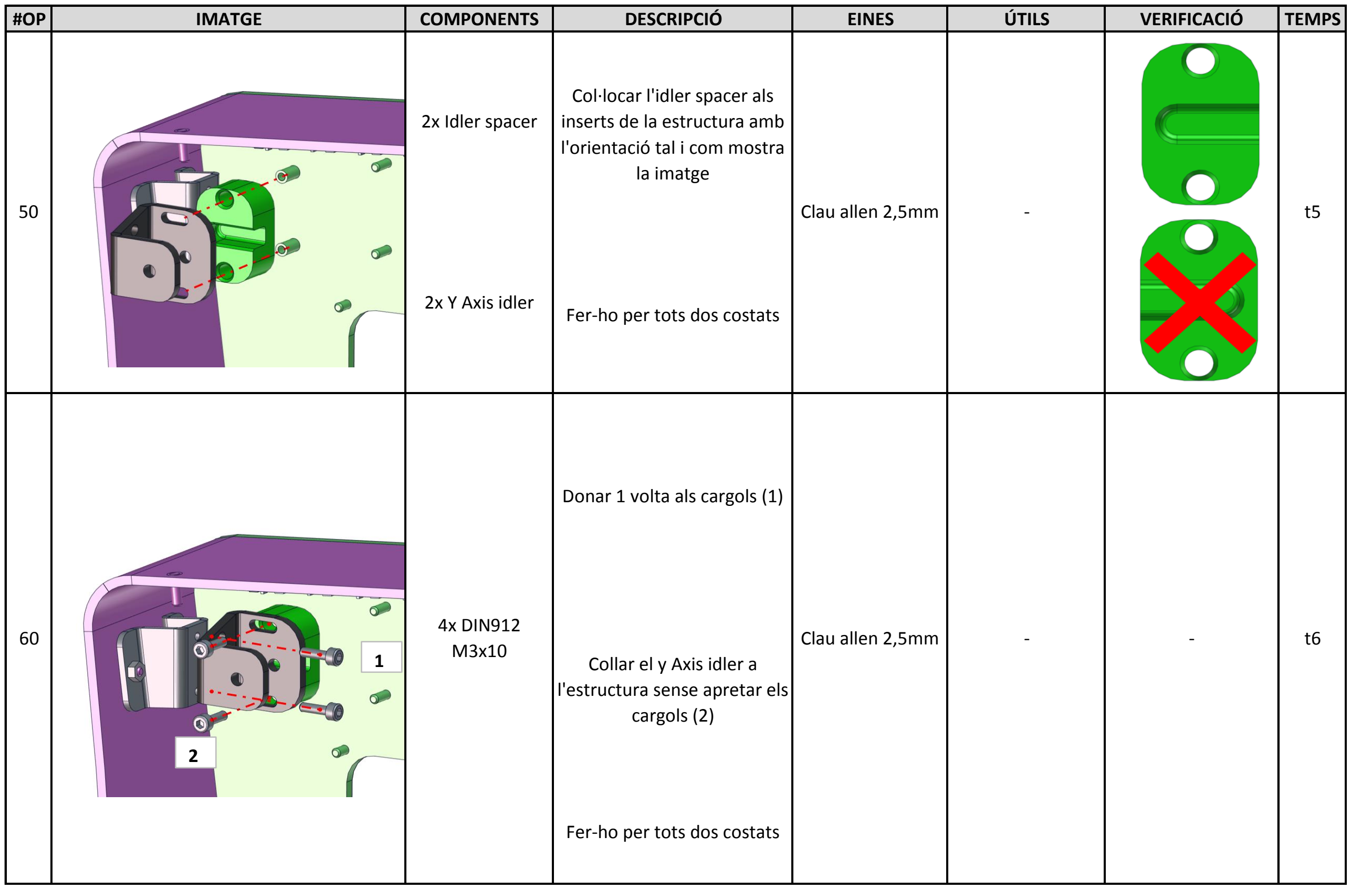
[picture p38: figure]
Col·locar l'idler spacer als inserts de la estructura amb l'orientació tal i com mostra la imatge; Fer-ho per tots dos costats; Donar 1 volta als cargols (1); Collar el y Axis idler a l'estructura sense apretar els cargols (2); Clau allen 2,5mm; 4x DIN912 M3x10; 2x Idler spacer; 2x Y Axis idler

#OP | IMATGE | COMPONENTS | DESCRIPCIÓ | EINES | ÚTILS | VERIFICACIÓ | TEMPS

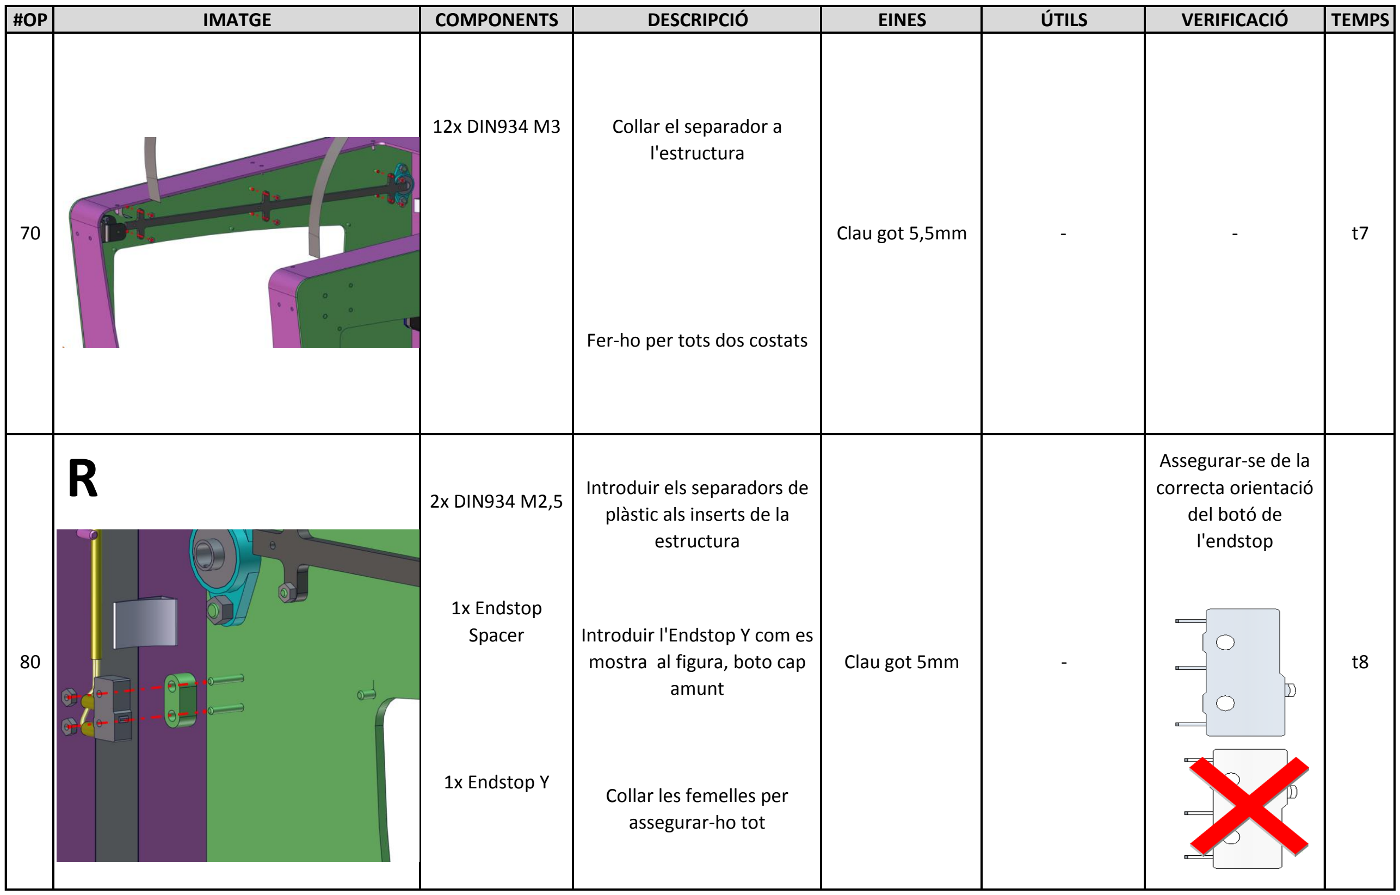
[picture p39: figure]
1x Endstop Spacer; Collar les femelles per assegurar-ho tot; 1x Endstop Y; Clau got 5mm; Assegurar-se de la correcta orientació del botó de l'endstop; 2x DIN934 M2,5; Introduir els separadors de plàstic als inserts de la estructura; Introduir l'Endstop Y com es mostra al figura, boto cap amunt; Collar el separador a l'estructura; Fer-ho per tots dos costats; Clau got 5,5mm; 12x DIN934 M3

#OP | IMATGE | COMPONENTS | DESCRIPCIÓ | EINES | ÚTILS | VERIFICACIÓ | TEMPS

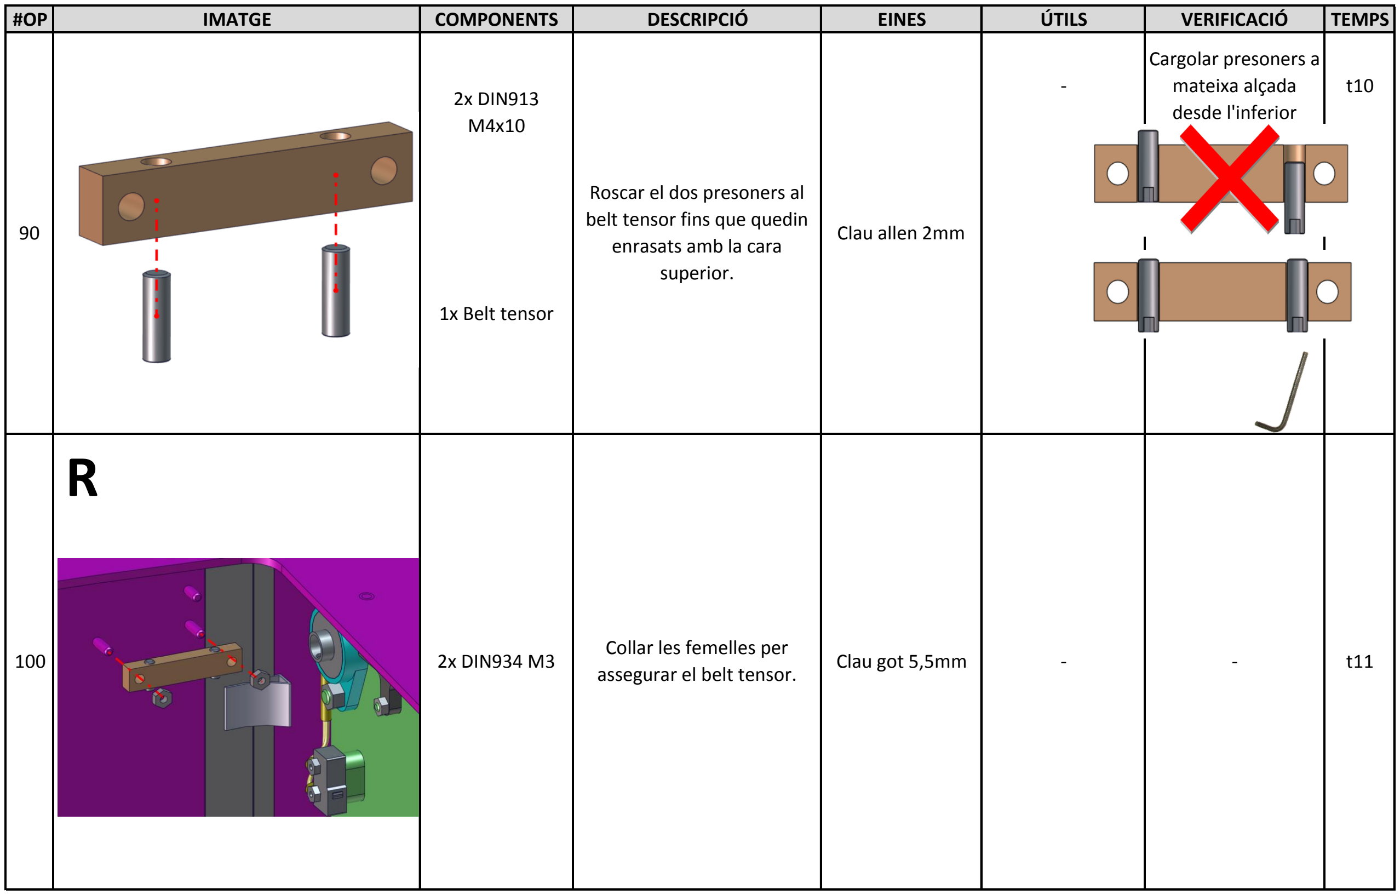
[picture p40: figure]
Roscar el dos presoners al belt tensor fins que quedin enrasats amb la cara superior.; 2x DIN913 M4x10; 1x Belt tensor; Collar les femelles per assegurar el belt tensor.; Clau allen 2mm; Clau got 5,5mm; 2x DIN934 M3; Cargolar presoners a mateixa alçada desde l'inferior

#OP | IMATGE | COMPONENTS | DESCRIPCIÓ | EINES | ÚTILS | VERIFICACIÓ | TEMPS

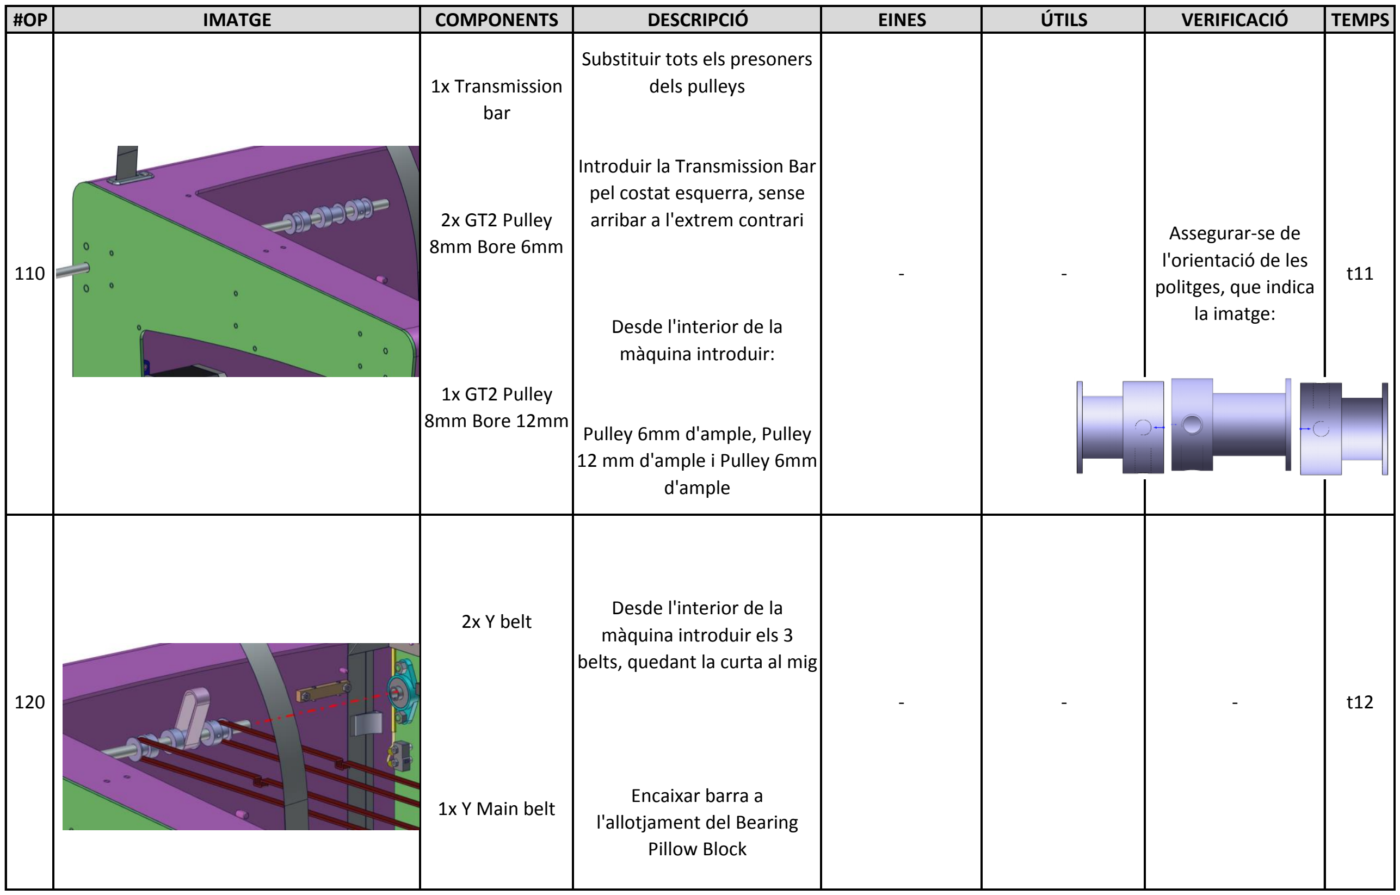
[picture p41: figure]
1x Transmission bar; 2x GT2 Pulley 8mm Bore 6mm; Substituir tots els presoners dels pulleys; Introduir la Transmission Bar pel costat esquerra, sense arribar a l'extrem contrari; Desde l'interior de la màquina introduir:; Pulley 6mm d'ample, Pulley 12 mm d'ample i Pulley 6mm d'ample; 1x GT2 Pulley 8mm Bore 12mm; Encaixar barra a l'allotjament del Bearing Pillow Block; Assegurar-se de l'orientació de les politges, que indica la imatge:; 2x Y belt; 1x Y Main belt; Desde l'interior de la màquina introduir els 3 belts, quedant la curta al mig

#OP | IMATGE | COMPONENTS | DESCRIPCIÓ | EINES | ÚTILS | VERIFICACIÓ | TEMPS

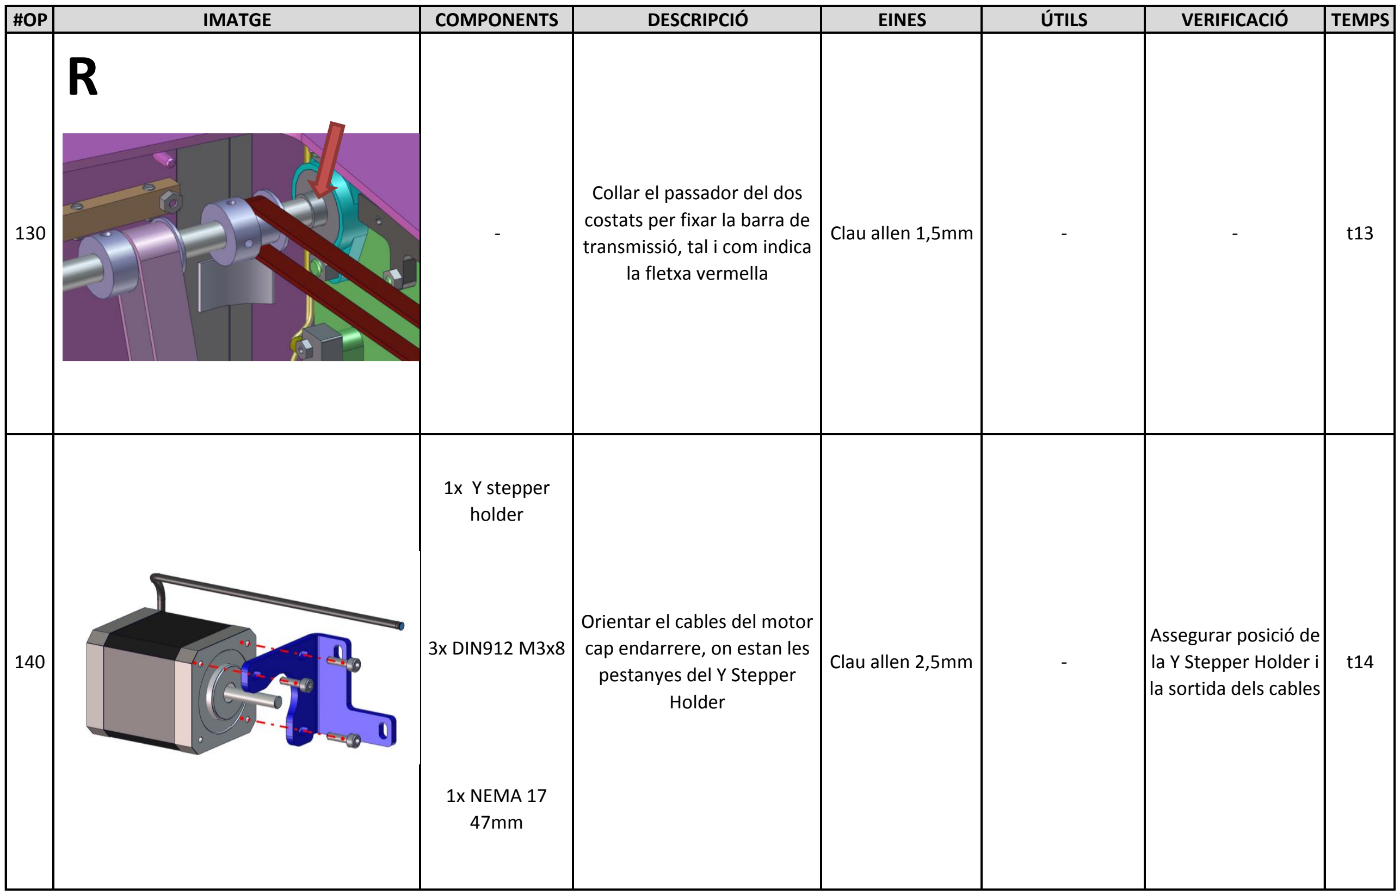
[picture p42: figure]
Assegurar posició de la Y Stepper Holder i la sortida dels cables; Clau allen 2,5mm; 1x Y stepper holder; Collar el passador del dos costats per fixar la barra de transmissió, tal i com indica la fletxa vermella; Clau allen 1,5mm; Orientar el cables del motor cap endarrere, on estan les pestanyes del Y Stepper Holder; 3x DIN912 M3x8; 1x NEMA 17 47mm

#OP | IMATGE | COMPONENTS | DESCRIPCIÓ | EINES | ÚTILS | VERIFICACIÓ | TEMPS

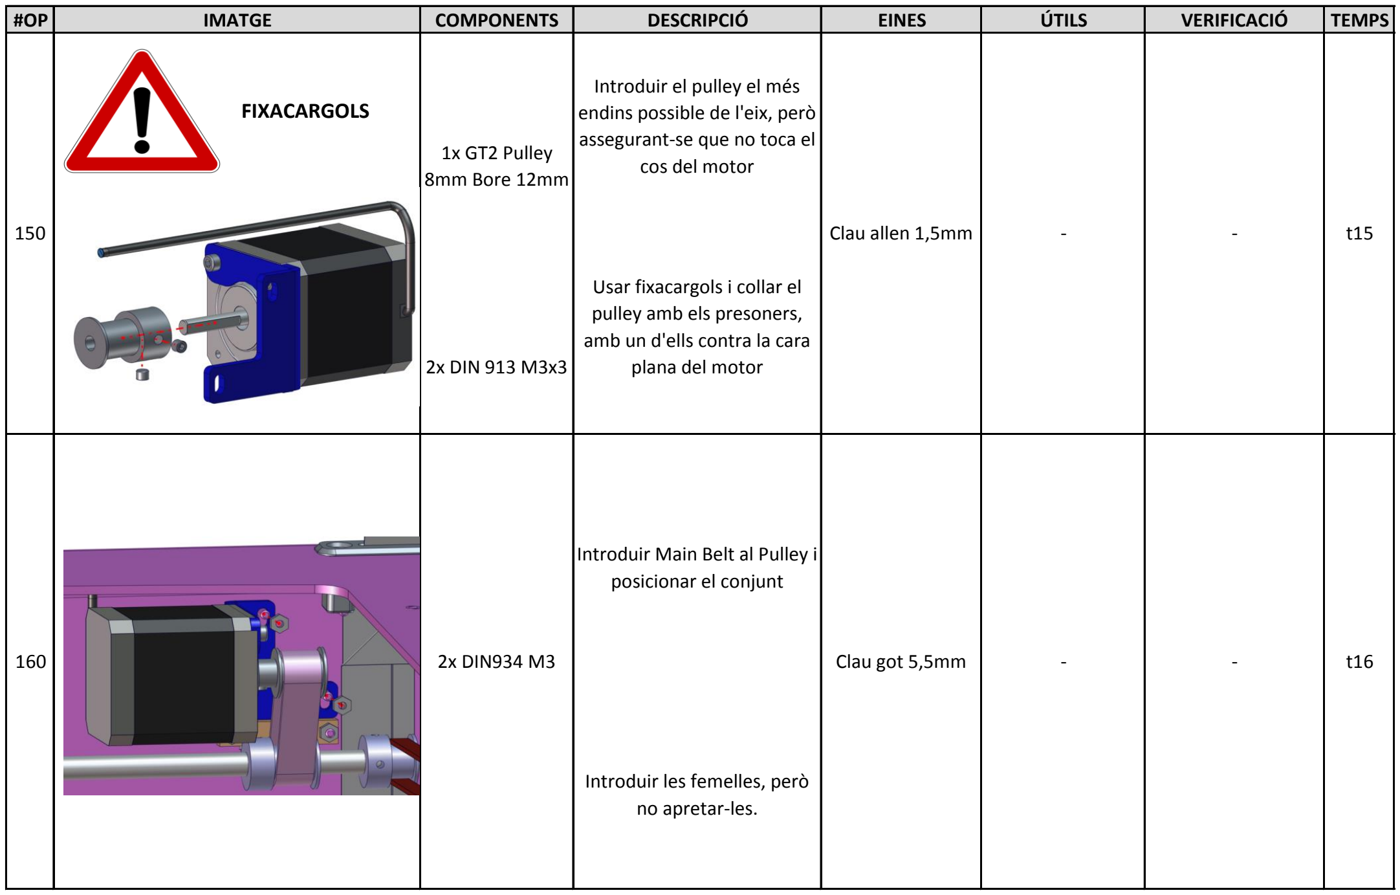
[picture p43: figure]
1x GT2 Pulley 8mm Bore 12mm; 2x DIN 913 M3x3; Clau got 5,5mm; Introduir les femelles, però no apretar-les.; Introduir Main Belt al Pulley i posicionar el conjunt; Introduir el pulley el més endins possible de l'eix, però assegurant-se que no toca el cos del motor; Usar fixacargols i collar el pulley amb els presoners, amb un d'ells contra la cara plana del motor; 2x DIN934 M3; Clau allen 1,5mm; FIXACARGOLS

#OP | IMATGE | COMPONENTS | DESCRIPCIÓ | EINES | ÚTILS | VERIFICACIÓ | TEMPS

#OP | IMATGE | COMPONENTS | DESCRIPCIÓ | EINES | ÚTILS | VERIFICACIÓ | TEMPS

Collar els cargols per fixar la Y guide

Fer-ho a tots dos costats

Clau allen 2,5mm | -

6x DIN912 M3x6

2x Y guide

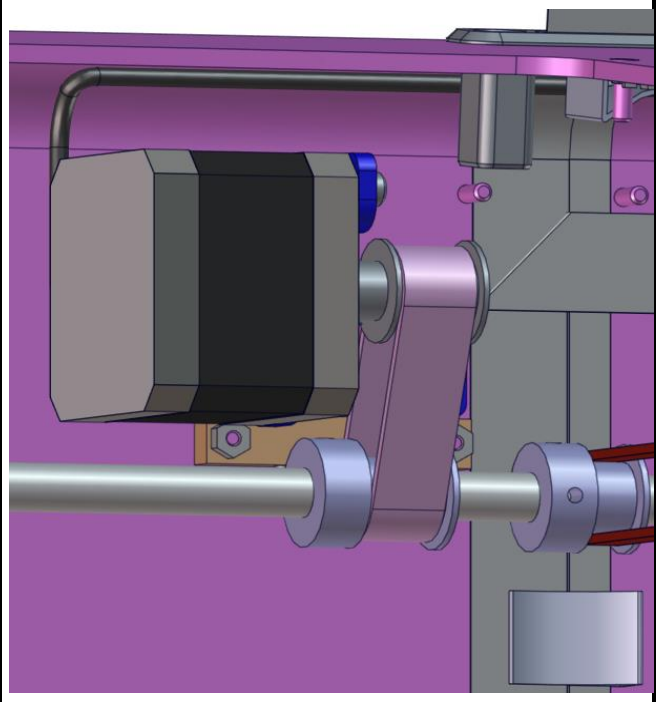
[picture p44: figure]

- | Clau allen 2mm | -

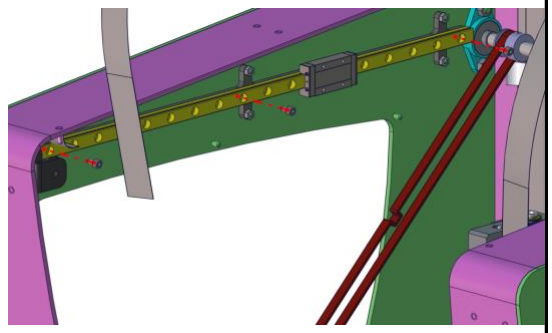
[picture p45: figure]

180 | - | t18

ATENCIÓ!! VIGILAR QUE ELS
PATÍ NO SURTI DE LA GUIA.
SI SURT, APARTAR
CONJUNT PER POSTERIOR
REVISIÓ
170 | - | t17

Comprovar la tensió de la
corretja i apretar les
femelles

Donar 3 voltes als passadors del Y Belt Tensioner

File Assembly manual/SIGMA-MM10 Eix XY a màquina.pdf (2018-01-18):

## MANUAL DE MUNTATGE

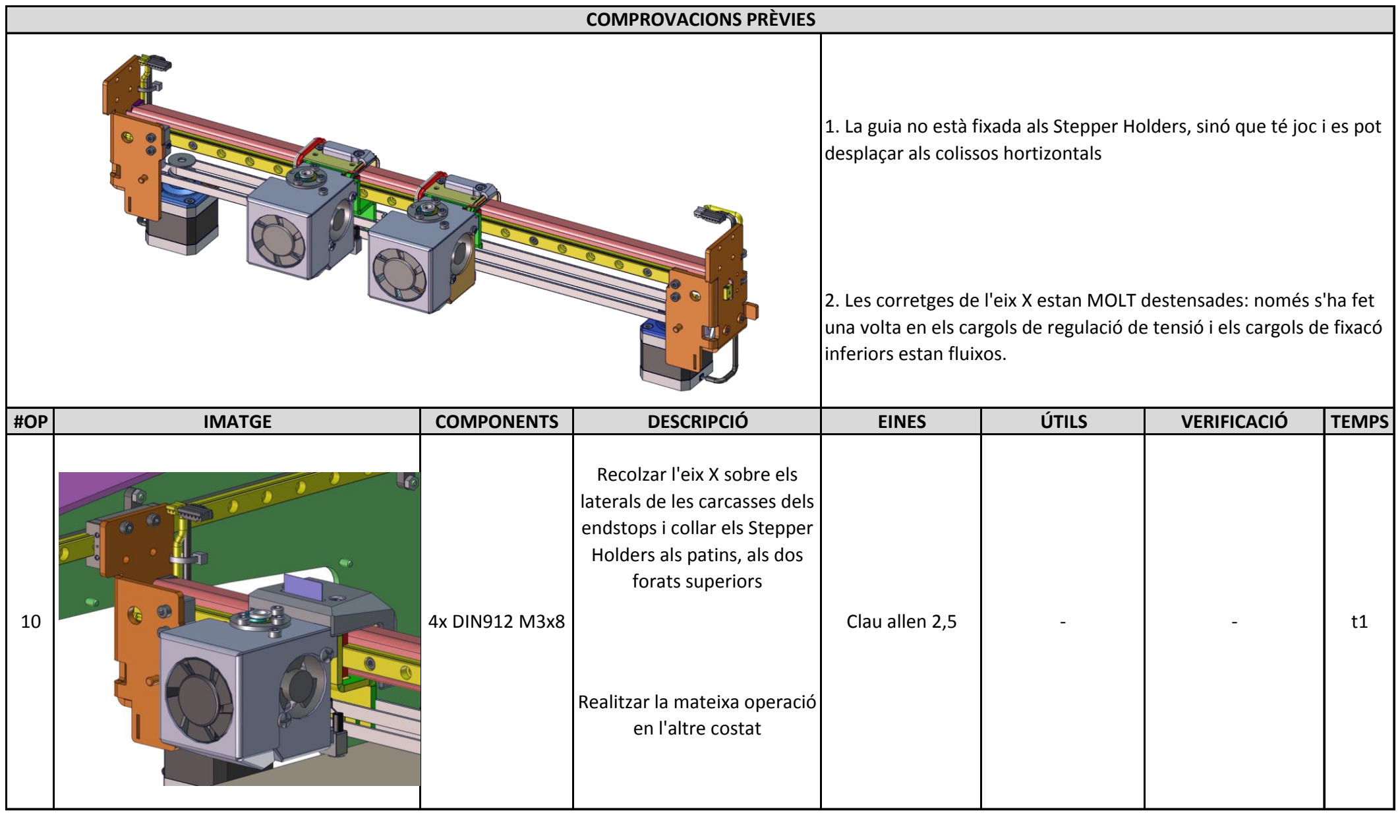
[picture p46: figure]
desplaçar als colissos hortizontals; inferiors estan fluixos.; Recolzar l'eix X sobre els laterals de les carcasses dels endstops i collar els Stepper Holders als patins, als dos forats superiors; 4x DIN912 M3x8; COMPROVACIONS PRÈVIES; Clau allen 2,5; Realitzar la mateixa operació en l'altre costat

#OP | IMATGE | COMPONENTS | DESCRIPCIÓ | EINES | ÚTILS | VERIFICACIÓ | TEMPS

1. La guia no està fixada als Stepper Holders, sinó que té joc i es pot
2. Les corretges de l'eix X estan MOLT destensades: només s'ha fet una volta en els cargols de regulació de tensió i els cargols de fixacó
CONJUNT | Eix XY a màquina
CODI DOCUMENT | SIGMA-MM10 | OPERARIS | 1 | DATA DOCUMENT | 18/01/2018
VERSIÓ DOCUMENT | v04 | TEMPS | T | CONTACTE | E. Pallarés

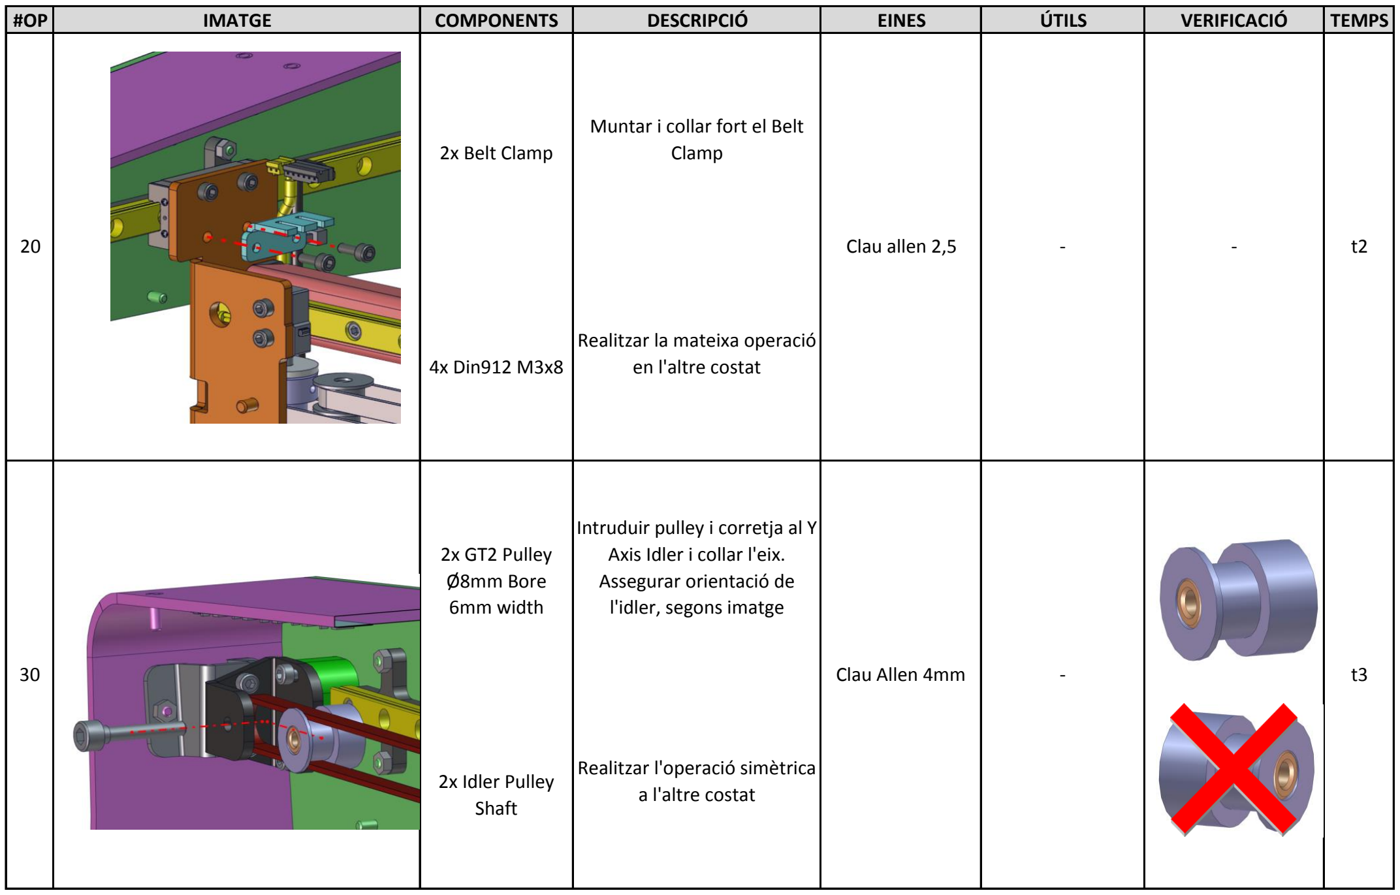
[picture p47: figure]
Muntar i collar fort el Belt Clamp; Clau allen 2,5; 2x Belt Clamp; 2x GT2 Pulley Ø8mm Bore 6mm width; 2x Idler Pulley Shaft; Intruduir pulley i corretja al Y Axis Idler i collar l'eix. Assegurar orientació de l'idler, segons imatge; Realitzar la mateixa operació en l'altre costat; Clau Allen 4mm; Realitzar l'operació simètrica a l'altre costat; 4x Din912 M3x8

#OP | IMATGE | COMPONENTS | DESCRIPCIÓ | EINES | ÚTILS | VERIFICACIÓ | TEMPS

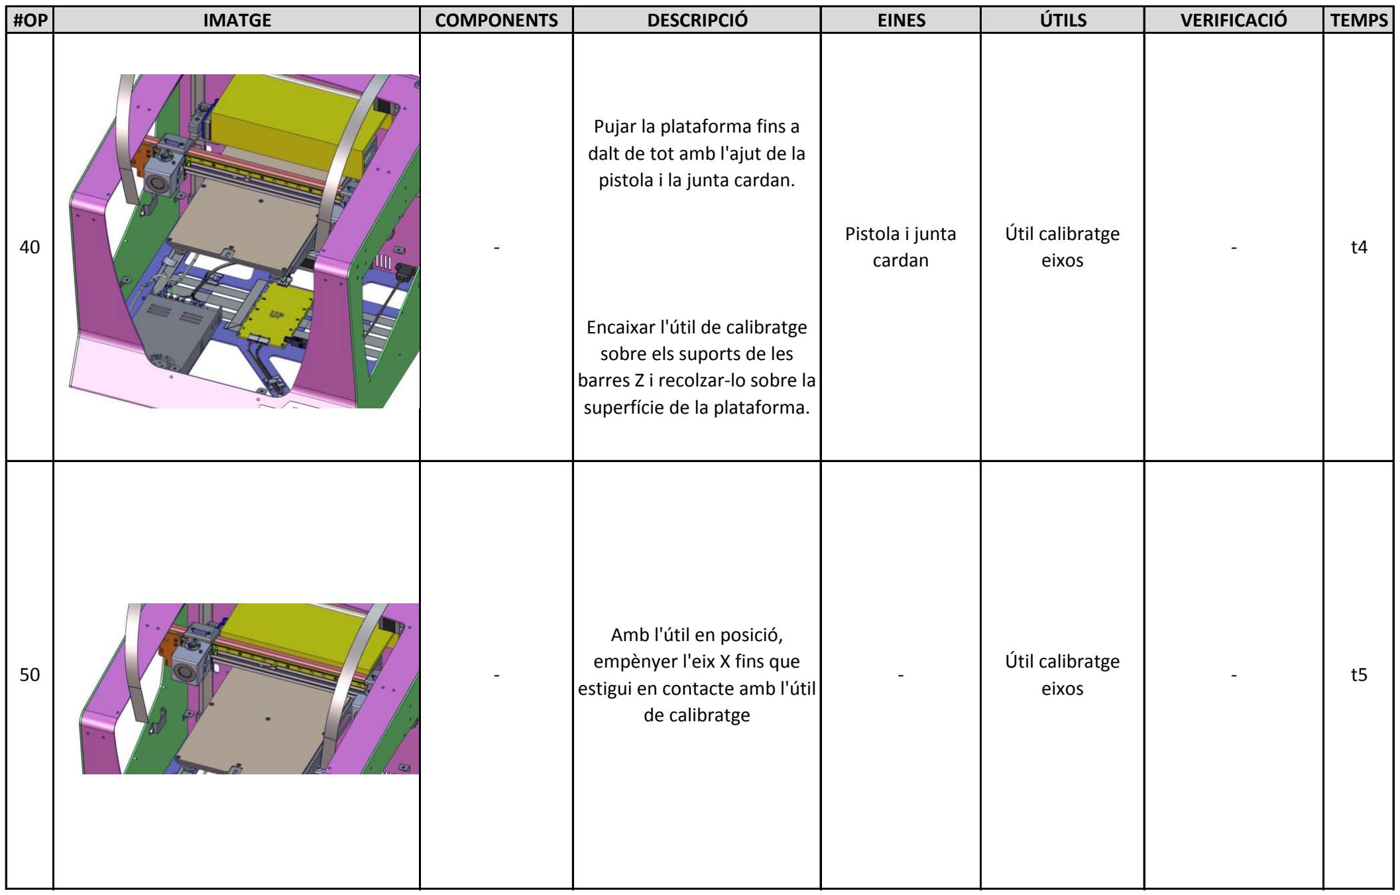
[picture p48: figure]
Pistola i junta; cardan; Pujar la plataforma fins a dalt de tot amb l'ajut de la pistola i la junta cardan.; Encaixar l'útil de calibratge sobre els suports de les barres Z i recolzar-lo sobre la superfície de la plataforma.; Útil calibratge eixos; Amb l'útil en posició, empènyer l'eix X fins que estigui en contacte amb l'útil de calibratge

#OP | IMATGE | COMPONENTS | DESCRIPCIÓ | EINES | ÚTILS | VERIFICACIÓ | TEMPS

Útil calibratge eixos; Fer el mateix a l'altre costat; Amb lútil i l'eix en posició, vigilant no perdre la posició i orientació dels pulleys, fixar la corretja tal i com mostra la imatge; Assegurar que s'ha passat la corretja tal i com mostra la imatge:; Amb l'útil i l'eix X en posició, girar els pulleys de la barra de transmissió fins que els presoners que els apretin siguin accessibles.; Fer-ho a totes dues politges de la barra de transimssió; Introduir l'útil de posició Pulleys Y per marcar ubicacions de les politges; Posició Pulleys Y

#OP | IMATGE | COMPONENTS | DESCRIPCIÓ | EINES | ÚTILS | VERIFICACIÓ | TEMPS

IMATGE; COMPONENTS; DESCRIPCIÓ; EINES; ÚTILS; VERIFICACIÓ; TEMPS; Útil calibratge eixos; Posició Pulleys Y; 4x DIN913 M4x4; Introduir l'útil de tensió de corretges Y entre l'Idler i el Tensioner.; Clau allen 2mm; Un cop assegurats els pulleys, validar paral·lelisme de l'eix X amb l'útil.; Amb el útil en posicio, apretar l'eix X contra ell, assegurant que recolza a tot el llarg i introduir l'útil de posició dels Pulleys Y.; Collar els presoners dels pulleys. UTILITZAR FIXACARGOLS!; Repetir a l'altre costat.; Retirar eix i extreure útils; Clau allen 2,5mm; Tensió corretges Y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

2x DIN913 M4x4; Moure eix Y endavant i enrere 4 vegades per assentar conjunt. Deixar-lo en posició centrada del recorregut; Apretar el motor X esquerre cap enfora, deformant una mica la xapa i collar els dos cargols encerclats.; Repetir a l'altre costat; Apretar els presoners del pulley de la corretja del motor de l'eix Y; Clau allen 2mm; Clau allen 2,5mm; Moviment i resistència uniforme a tot el llarg del recorregut eix Y.; FIXACARGOLS

#OP | IMATGE | COMPONENTS | DESCRIPCIÓ | EINES | ÚTILS | VERIFICACIÓ | TEMPS

Introduir l'útil de tensió de corretges X entre l'Idler l'Stepper Holder; Repetir a l'altre costat; Tensar les corretges cargolant els cargols de regulació fins a la distància marcada per l'útil; Clau allen 2,5mm; Moviment i resistència uniforme a tot el llarg del recorregut eix Y.; Fixar l'idler collant fort els cargols inferiors, encerclats

#OP | IMATGE | COMPONENTS | DESCRIPCIÓ | EINES | ÚTILS | VERIFICACIÓ | TEMPS

120 | - | Clau allen 2,5mm | Tensió corretges X | - | t12

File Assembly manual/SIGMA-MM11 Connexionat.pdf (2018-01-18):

## MANUAL DE MUNTATGE

una petita estrabada; 1x Main Board; 4x Plastic Spacers 3,2mm; 4x DIN934 M3; 3x DIN125 M3 Poliamida; Introduir els separadors de plàstic als perns de l'estructura; Introduir la Main Board; Sense volandera; Collar conjunt amb les femelles; Introduir les 3 volanderes de plàstic. El pern al costat del port USB va SENSE; Clau de got 5,5mm

#OP | IMATGE | COMPONENTS | DESCRIPCIÓ | EINES | ÚTILS | VERIFICACIÓ | TEMPS

2) Orientar el cable amb els contactes metàl·lics cap a la PCB 1) Obrir el clip del connector. Fer-ho cuidadosament amb les ungles
CONJUNT | Connexionat i Cobertes
CODI DOCUMENT | SIGMA-MM11 | OPERARIS | 1 | DATA DOCUMENT | 18/01/2018
VERSIÓ DOCUMENT | v04 | TEMPS | T | CONTACTE | E. Pallarés

INSTRUCCIONS DE CONNEXIONAT DE CABLES PLANS
3) Introduir el cable fins al fons del connector i tancar el clip amb les ungles. Assegurar que el cable està recte i que està ben connectat amb

Connectar els 8 cables plans; a la Main Board; Verificar que els cables no estan torts i que el clip està ben tancat.; Connectar el cable DC Power i el cable d'alumentació del Hot Bed. Només hi ha una posició possible de connexionat

#OP | IMATGE | COMPONENTS | DESCRIPCIÓ | EINES | ÚTILS | VERIFICACIÓ | TEMPS

Connectar el cable USB. Només hi h auna posició possible de connexionat; Connectar el cable de la pantalla al connector de la dreta. Només hi ha una posició possible de connexionat; Connectar el cable del mòdul SD al connector de l'esquerra. Només hi ha una posició possible de connexionat

#OP | IMATGE | COMPONENTS | DESCRIPCIÓ | EINES | ÚTILS | VERIFICACIÓ | TEMPS

Clau de got 5,5mm; Connector; totalment tancat!; Connectar els cables dels LEDs de l'esquerra al connector superior.; Connectar els cables dels LEDs de la dreta al connector inferior.; En tots dos casos, el cable vermell, a l'esquerra (veure imatge verificació); Introduir els Spacers als perns; Connectar el cable pla de l'eix Z a l'Stepper Driver; Connectar el cable del motor a l'Stepper Driver. Només hi ha una posició possible de connexionat; Introduir les volanderes i collar amb les femelles; 1x Stepper Driver; 2x Ariston Spacer 3mm; 2x DIN934 M3; 2x DIN125 M3 Poliamida

#OP | IMATGE | COMPONENTS | DESCRIPCIÓ | EINES | ÚTILS | VERIFICACIÓ | TEMPS

Introduir el Driver Spacer als perns; Connectar el cable pla E0 a l'Stepper Driver; 1x Extruder Driver Cover; 2x DIN934 M3; Collar amb les femelles; Introduir Extruder Driver Cover; Introduir 2 separadors a cada pern; Clau de got 5,5mm; Connector; totalment tancat!; Connectar el cable del motor a l'Stepper Driver. Només hi ha una posició possible de connexionat; 1x Driver Spacer; 1x Stepper Driver

#OP | IMATGE | COMPONENTS | DESCRIPCIÓ | EINES | ÚTILS | VERIFICACIÓ | TEMPS

Clau de got 5,5mm | - | - | t9 4x Plastic Spacer

Connector; totalment tancat!; Clau de got 5,5mm; 1x Stepper Driver; Repetir operacions 90 i 100 en l'altre costat; 1x Driver Spacer; 2x DIN934 M3; 2x DIN125 M3 Poliamida; Introduïr el Driver Spacer als perns; Connectar cable pla Y a l'Stepper Driver; Connectar endstop Y a l'Stepper Driver. Només hi ha una possible posició de connexionat; Connectar motor a l'Stepper Driver. Només hi ha una posició de connexionat; Introduir les volanderes de plàstic i collar amb les femelles; 1x Extruder Driver Cover; 4x Plastic Spacer

#OP | IMATGE | COMPONENTS | DESCRIPCIÓ | EINES | ÚTILS | VERIFICACIÓ | TEMPS

Connector; totalment tancat! 2x DIN912 M3x8; Connectar endstop X0 a l'Stepper Driver. Només hi ha una posició possible de connexionat; Connectar motor X0 a l'Stepper Driver. Només hi ha una posició possible de connexionat; Collar conjunt al patí; Collar el conjunt tal i com; 1x X Stepper Driver Holder Left; 1x Driver Spacer; 1x Stepper Driver; 2x DIN912 M3x6; 2x DIN125 M3 Poliamida; Connectar cable Pla X0 a l'Stepper Driver

#OP | IMATGE | COMPONENTS | DESCRIPCIÓ | EINES | ÚTILS | VERIFICACIÓ | TEMPS

mostra la figura | Clau Allen 2,5mm | - | - | t12

Collar el conjunt tal i com; mostra la figura; Clau Allen 2,5mm; 1x X Stepper Driver Holder Right; 1x Driver Spacer; 1x Stepper Driver; 2x DIN912 M3x6; 2x DIN125 M3 Poliamida; 2x DIN912 M3x8; Connectar cable Pla X1 a l'Stepper Driver; Connectar endstop X1 a l'Stepper Driver. Només hi ha una posició possible de connexionat; Connectar motor X1 a l'Stepper Driver. Només hi ha una posició possible de connexionat; Collar conjunt al patí

#OP | IMATGE | COMPONENTS | DESCRIPCIÓ | EINES | ÚTILS | VERIFICACIÓ | TEMPS

Connector; totalment tancat!; 4x DIN912 M3x10; Clau Allen 2,5mm; Collar la Conexion Cover tot vigilant que els cables hi queden dins i que no es pincen amb els cargols; Repetir a tots dos capçals; Introduir el cable per la ranura de la Conexion Cover en l'orientació mostrada a la imatge; Clau allen 2mm; Repetir als dos capçals; 2x Conexion Cover; 2x Flat Cable Clip; 2x DIN7991 M3x10; Connectar el cable; Pinçar el cable pla amb el Flat Cable Clip i collar fort. Assegurar que està ben recte

#OP | IMATGE | COMPONENTS | DESCRIPCIÓ | EINES | ÚTILS | VERIFICACIÓ | TEMPS

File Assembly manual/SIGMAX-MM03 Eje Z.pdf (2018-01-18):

## MANUAL DE MONTAJE

2x Flanged Linear Bushing; 8x DIN125 M3; 8x DIN912 M3x6; Con arandela entre medio, apretar los tornillos de los rodamientos en la Lower Platform; Llave Allen 2,5mm; 1xZ Nut; 3X DIN912 M3; 3x DIN912 M3X8; Con arandela entre medio, apretar los tornillos un poco de forma que quede con juego

#OP | IMAGEN | COMPONENTES | DESCRIPCIÓN | HERRAMIENTAS | ÚTILES | VERIFICACIÓN | TIEMPOS

CONJUNTO | Eje Z
CODIGO DOCUMENTO | SIGMAX-MM03 | OPERARIOS | 1 | FECHA DOCUMENTO | 16/01/2018
VERSIÓN DOCUMENTO | v01 | TEMPOS | T | CONTACTO | M.UCERO

IMAGEN; COMPONENTES; DESCRIPCIÓN; HERRAMIENTAS; ÚTILES; VERIFICACIÓN; TIEMPOS; Asegurar que no hay deformación del corcho por haber apretado demasiado los tornillos; Encarar primero todos los tornillos. Apretar en el orden indicado.; 1x Reinforcement; 1x Lower platform; Destorinillador electrico punta PHILIPS PH2"; 1x Upper Platform; 2x Heated Bed; 18x DIN7991 M3x6; Colocar los tornillos al Upper Platform haciendo un sándwich entre Hotbed, Cork y Upper Platform; Llave Allen 2mm; 2x Cork

| | 9x DIN7981 (3,2x9,5)mm | No apretar la placa reinforcement a la Lower Platform. Posicionar permitiendo movimiento.

#OP | IMAGEN | COMPONENTES | DESCRIPCIÓN | HERRAMIENTAS | ÚTILES | VERIFICACIÓN | TIEMPOS

t50

Conectar el cable del Hot
Bed en las dos camas
calientes , obligando al
cable a salir por la parte posterior de las chapas. El conector con los cuatro
cables rojo,2azules,negro
va conectado en el la zona central de la cama caliente
50 | Hot Bed Cable
3x Printing surface spring | Colocar un muelle en cada inserto y encajar los insertos de la Upper Platform en la Lower Platform.
2x Thumbscrew | Enroscar los thumbsrews en los 2 pernos frontales, introducir la galga cara 'F' (Frente) y enroscar hasta que la toque.
1x DIN985 M5 | Enroscar con la hembra autoblocante en el perno posterior, introducir la galga cara 'B' (Back) y enroscar hasta que la toque.

Galga muelles Llave de tubo 8mm

- t40

El conector con
cable azul va
conectado en la
parte central de
la cama caliente

40

4x Hot Bed Cable Clip; 4x DIN912 M4; Atrapar los cables con los clips y forzarlo a seguir la ruta marcada en la imagen.; Colocar los clips en la lower platform; Llave de vaso 7mm

#OP | IMAGEN | COMPONENTES | DESCRIPCIÓN | HERRAMIENTAS | ÚTILES | VERIFICACIÓN | TIEMPOS

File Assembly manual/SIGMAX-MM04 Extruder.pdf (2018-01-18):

## MANUAL DE MONTAJE

1x extruder body right; CONJUNTO; Extruder; Útil para evitar deformación de los Extruder Body; Prensa manual; 1x Extruder body left; 4x Pneufit Coupling; Repetir los mismos procesos para el Extruder Body Right; Colocar el pneufit coupling y aplicar fuerza con una prensa para que quede fijado; Dar la vuelta al Extruder Body left y fijar el otro pneufit coupling de la misma manera.

CODIGO DOCUMENTO | SIGMAX-MM04 | OPERARIOS | 1 | FECHA | 16/01/2018
VERSIÓN DOCUMENTO | v05 | TIEMPOS | T | CONTACTO | E. Pallarés
#OP | IMAGEN | COMPONENTES | DESCRIPCIÓN | HERRAMIENTAS | ÚTILES | VERIFICACIÓN | TIEMPOS

| | | Colocar el útil en el Body Extruder Left

Maza de nylon; 1xTensor Right; 2x Drived Gear; 2x pasador 4x24mm; Verificar que el Drived Gear la parte mas ancha queda como muestra la imagen; Útil para evitar deformación del Tensor; Pasar el pasador ayudandose con un martillo de Nylon para que quede fijado.; Repetir el mismo proceso para el Tensor Right

#OP | IMAGEN | COMPONENTES | DESCRIPCIÓN | HERRAMIENTAS | ÚTILES | VERIFICACIÓN | TIEMPOS

| | 1xTensor Left | Colocar el Tensor left en el util quedando el Drived Gear entre medio de los dos

Separador Drive Gear Extruder llave allen 2mm; Comprobar que el prisionero está roscado contra la cara plana del Nema 17; 2x Cable extruder cable; Colocar el extruder cable en; el motor

#OP | IMAGEN | COMPONENTES | DESCRIPCIÓN | HERRAMIENTAS | ÚTILES | VERIFICACIÓN | TIEMPOS

| | 1x Nema 17 60mm | Posicionar el útil hasta hacer contacto con el eje del motor
| | 1x Driving Gear 1x DIN913 M4x3 | Apoyar el Driving Gear sobre el útil. Roscar el prisionero todo asegurándose de que se aprieta la cara plana del Nema 17

1xExtruder Body Left; 1x Extruder Stepper Holder; 1x Conjunto Extruder Body Left y Eextruder Tension Left; 1x Conjunto Nema 17 y Driving Gear; Utilizar los tornillos como guía para hacer paquete del extruder Stepper Holder, el Extruder Body Left y los subconjuntos montados anteriormente; Verificar posicion de la pestaña del Extruder Tension Right cercana a el Nema 17; 1x Extruder Tension Left; Posicionar el Extruder Tension Left como muestra la imagen; Repasar orientación de la salida de los cables y de las pestañas del Extruder Stepper Holder y Extruder Tension Left.; Asegurar concentricidad del Driving Gear con los orificios del conjunto montado; llave Allen 2,5mm; Roscar los tornillos asegurando que la orientación de las pestañas del Extruder Stepper Holder es perpendicular a la salida de los cables del Nema 17 3x DIN912 M3x35

#OP | IMAGEN | COMPONENTES | DESCRIPCIÓN | HERRAMIENTAS | ÚTILES | VERIFICACIÓN | TIEMPOS

Pasar el tornillo a traves del Extruder Body colocar el spring y roscar el Purger Button; 1x DIN933 M4x50; 1xSpring; 2x Pneufit Coupling; 1x Purger Button; Introducir los Pneufit Coupling presionando hasta encajar en los agujeros

#OP | IMAGEN | COMPONENTES | DESCRIPCIÓN | HERRAMIENTAS | ÚTILES | VERIFICACIÓN | TIEMPOS

1x Conjunto Nema 17 y Driving Gear; 1x Conjunto Extruder Body Left y Eextruder Tension Left; 1xExtruder Body Right; 1x Extruder tension left; Utilizar los tornillos como guía para hacer paquete del extruder Stepper Holder, el Extruder Body Left y los subconjuntos montados anteriormente; Repasar orientación de la salida de los cables y de las pestañas del Extruder Stepper Holder y Extruder Tension Left.; 3x DIN912 M3x35; Roscar los tornillos asegurando que la orientación de las pestañas del Extruder Stepper Holder es la misma que la salida de los cables del Nema 17; Asegurar concentricidad del Driving Gear con los orificios del conjunto montado; llave Allen 2,5mm; 1x Extruder Stepper Holder; Posicionar el Extruder Tension Right como muestra la imagen; Verificar posicion de la pestaña del Extruder Tension Right cercana a el Nema 17

#OP | IMAGEN | COMPONENTES | DESCRIPCIÓN | HERRAMIENTAS | ÚTILES | VERIFICACIÓN | TIEMPOS

#OP | IMAGEN | COMPONENTES | DESCRIPCIÓN | HERRAMIENTAS | ÚTILES | VERIFICACIÓN | TIEMPOS


| | 1x DIN933 M4x50
- | - | t100

Introducir los Pneufit
Coupling presionando hasta encajar en los agujeros


100 | -

90

1x Purger Button

2x Pneufit
Coupling

Pasar el tornillo a traves del Extruder Body colocar el
Spring y roscar el Purger
Button

1xSpring
- | - | t90

R

R

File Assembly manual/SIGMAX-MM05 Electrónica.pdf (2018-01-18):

## MANUAL DE MONTAJE

Llave de vaso 8mm torneada; Llave de vaso; 8mm torneada; Unir el Bearing Pillow Block con las hembras. Golpear con maza de nylon en su caso; 2x DIN934 M5; 1x Bearing pillow Block; Verificar la planitud de los rodamientos y que su giro dentro del encapsulado no es excéntrico. Enderezar con la ayuda de una barra en su caso

#OP | IMAGEN | COMPONENTES | DESCRIPCIÓN | HERRAMIENTAS | ÚTILES | VERIFICACIÓN | TIEMPOS

| | 1x Bearing pillow Block | Verificar la planitud de los rodamientos y que su giro dentro del encapsulado no es excéntrico. Enderezar con la ayuda de una barra en su caso
CONJUNTO | Electrónica
CODIGO DOCUMENTO | SIGMAX-MM05 | OPERARIOS | 1 | FECHA DOCUMENTO | 16/01/2018
VERSIÓN DOCUMENTO | v01 | TIEMPOS | T | CONTACTO | Mikel Ucero

No dejar las tuercas apretadas, para su posterior alineamiento de la Transmision Bar; Posicionar la plantilla en la parte izquierda de la estructura, haciendo coincidir los agujeros con los pernos; 1xDry - running mounted slave; 1x Y axis pillow bearing spacer; Plantilla Posterior Left SigmaX; Llave de vaso 5,5mm torneada; 2x DIN 934 M3

#OP | IMAGEN | COMPONENTES | DESCRIPCIÓN | HERRAMIENTAS | ÚTILES | VERIFICACIÓN | TIEMPOS

Retirar la pegatina de las tachuelas y posicionarlas en los agujeros marcados con un triangulo en la plantilla en la posicion que marca el triangulo grabado; No colocar tachuelas en los agujeros que no haya triangulo; Posicionar la plantilla en la parte derecha de la estructura, haciendo coincidir los agujeros con los pernos; Plantilla Posterior Right; Plantilla Posterior Left; Retirar con cuidado la Plantilla Posterior; 3x Flat Cable Clip

#OP | IMAGEN | COMPONENTES | DESCRIPCIÓN | HERRAMIENTAS | ÚTILES | VERIFICACIÓN | TIEMPOS

Posicionar la plantilla en la parte inferior derecha de la estructura, haciendo coincidir los agujeros con los pernos; Plantilla Posterior Right; No colocar tachuelas en los agujeros que no haya triangulo; 3x Flat cable clip; Retirar la pegatina de las tachuelas y posicionarlas en los agujeros marcados por la plantilla en la posicion que marca el triangulo grabado; Retirar con cuidado la Plantilla Posterior; Plantilla inferior derecha

#OP | IMAGEN | COMPONENTES | DESCRIPCIÓN | HERRAMIENTAS | ÚTILES | VERIFICACIÓN | TIEMPOS

Retirar la pegatina de las tachuelas y posicionarlas en los agujeros marcados por la plantilla en la posicion que marca el triangulo grabado; Retirar con cuidado la Plantilla inferior; Posicionar la plantilla en la parte inferior izquierda de la estructura, haciendo coincidir los agujeros con los pernos; Plantilla inferior izquierda; No colocar tachuelas en los agujeros que no haya triangulo; 3x Flat Cable; Clips; Plantilla inferior derecha

#OP | IMAGEN | COMPONENTES | DESCRIPCIÓN | HERRAMIENTAS | ÚTILES | VERIFICACIÓN | TIEMPOS

2xFlat Cable Clip; Retirar la pegatina de las tachuelas y posicionarlas en la posición que se muestra en la imagen; Realizar la misma operación de manera simetrica en el lado opuesto; Retirar la pegatina de las tachuelas y posicionarlas en los agujeros marcados por la plantilla en la posicion que; marca el triangulo grabado; Plantilla inferior derecha; No colocar tachuelas en los agujeros que no haya triangulo; Retirar con cuidado la Plantilla inferior; 2x Flat cable clips

#OP | IMAGEN | COMPONENTES | DESCRIPCIÓN | HERRAMIENTAS | ÚTILES | VERIFICACIÓN | TIEMPOS

llave de tubo de 3mm; 1x Screen positioner; 1x LCD Touchscreen; 2x Front screen holder; 2x DIN934 M3; Colocar el spacer sobre la pantalla y quitar la pegatina de esta y pegar sobre la estructura; Ubicar los space holder en la parte interior de la carcasa en sus respectivos pernos y apretar las tuercas; 1x LCD Flex Cable; (1)Estirar la pestaña negra conectar el cable plano en la orientación de la imagen y (2)empujar la pestaña para que el cable quede bien sujeto; Cercionarse de que los pines del cable estan en la orientación de la imagen

#OP | IMAGEN | COMPONENTES | DESCRIPCIÓN | HERRAMIENTAS | ÚTILES | VERIFICACIÓN | TIEMPOS

1xLCD PCB Adapter; Cinta de doble cara; Colocar una tira de cinta de doble cara a la pcb y fijar a la estructura; la imagen conectar el otro extremo del cable plano en el conector en la orientacion indicada en las imágenes

#OP | IMAGEN | COMPONENTES | DESCRIPCIÓN | HERRAMIENTAS | ÚTILES | VERIFICACIÓN | TIEMPOS

| | | | | | Cercionarse de que los pines del cable estan en la orientación de

2x DIN934 M3; 4xDIN 125 M3; Manteniendo la orientación de la máquina colocar en la estructura el modulo de la SD ensamblado anteriormente; Apretar fuerte las dos tuercas; llave de tubo 5,5mm; llave allen 2,5mm; Colocar el modulo junto con el separador de plastico a la chapa SD holder; 3x DIN912 M3x8; 1X SD spacer; 1x SD Holder; 1x SD Module

#OP | IMAGEN | COMPONENTES | DESCRIPCIÓN | HERRAMIENTAS | ÚTILES | VERIFICACIÓN | TIEMPOS

Repetir en el otro costado; 2x Front LED connector clamp; 2x DIN934 M3; Posicionar el Front LED connector clamp , pero sin apretar de manera quese pueda desplazar la tira LED; llave de tubo 5,5mm; 4x Plain Flat cable holder; 6x DIN934 M3; Posicionar los plain Flat cable holders , sin apretar las tuercas; Ajustar la posición de la tira LED y los Plain Flat cable holders de manera que éstos sujeten la parte plana de la tira de LED; Retirar el protector de las tiras y aplicar el adhesivo

#OP | IMAGEN | COMPONENTES | DESCRIPCIÓN | HERRAMIENTAS | ÚTILES | VERIFICACIÓN | TIEMPOS

| | 2x LED | Introcucir los cables de la tira led entre Introduir els cables de la tira de LED entre el perno, dejando 3mm a la pared lateral y 1 al interior de la maquina

#OP | IMAGEN | COMPONENTES | DESCRIPCIÓN | HERRAMIENTAS | ÚTILES | VERIFICACIÓN | TIEMPOS


| | | Pasar el cable del LEDs por la ruta indicada de la imagen

Repetir el otro costado

- | - | - | t200


210 | - | - | - | - | t210

Pasar el cable del LED
izquierdo por la ruta
indicada de la imagen

Pasar el cable del LED derecho por la ruta indicada de la imagen; orientación de las fuentes de alimentación; 8x DIN912 M4x6; 2x Power Supply; Posicionar la estructura sobre la parte superior para facilitar el montaje de los siguientes pasos; Orientar la fuente de alimentación y los conectores sobre la parte posterior de la máquina (ver verificación); Colocar 8 tornillos. En el caso de que por culpa del punto de la soldadura no llegue poner un tornillo mas largo; Llave allen 3,5mm

#OP | IMAGEN | COMPONENTES | DESCRIPCIÓN | HERRAMIENTAS | ÚTILES | VERIFICACIÓN | TIEMPOS

1x Relay; 2x DIN934 M3; Posicionar la estructura sobre la base; Orientar el Relay y colocar en los pernos correspondientes (ver verificación); Colocar las 2 tuercas y apretar para que le relay quede fijo en su posición; llave de tubo 5,5mm; Orientación Relay. Canal 1 y 2 orientado al lado iquierdo y 3, 4 al lado derecho

#OP | IMAGEN | COMPONENTES | DESCRIPCIÓN | HERRAMIENTAS | ÚTILES | VERIFICACIÓN | TIEMPOS

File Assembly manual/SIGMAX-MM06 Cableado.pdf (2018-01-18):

## MANUAL DE MONTAJE

Maza de nylon (si se necesita); Seguir la ruta marcada del cable rojo a lo largo de las tachuelas; DESCRIPCIÓN; 2x Bowden Exit; Encarar los Bowden Exit en la estructura, en la orientación mostrada en la imagen. Sin encajar del todo; Cable plano de 20 vías; Hotend 0

#OP | IMAGEN | COMPONENTES | HERRAMIENTAS | ÚTILES | VERIFICACIÓN | TIEMPOS

CONJUNTO | Cableado
CODIGO DOCUMENTO | SIGMAX-MM06 | OPERARIOS | 1 | FECHA DOCUMENTO | 16/01/2018
VERSIÓN DOCUMENTO | v01 | TIEMPOS | T | CONTACTO | Mikel Ucero

DESCRIPCIÓN; Seguir la ruta marcada del cable en rojo a lo largo de las tachuelas; Cable Plano 15 vias

#OP | IMAGEN | COMPONENTES | HERRAMIENTAS | ÚTILES | VERIFICACIÓN | TIEMPOS

llave de tubo 5,5mm; DESCRIPCIÓN; Desllizar el cable, haciéndolo pasar por debajo de las piezas de plástico. Collar fuerte las tuercas para fijar posición; Seguir la ruta marcada del cable en rojo a lo largo de las tachuelas

#OP | COMPONENTES | HERRAMIENTAS | ÚTILES | VERIFICACIÓN | TIEMPOS | TEMPS

2x DIN934 M3; Seguir la ruta marcada del cable en rojo a lo largo de las tachuelas; llave de tubo 5,5mm; 1x Curve Flat Cable Holder; Apretar el Curve Flat Cable Holder aprisionando los dos cables planos; Cable Plano 15 vias

#OP | IMAGEN | COMPONENTES | DESCRIPCIÓN | HERRAMIENTAS | ÚTILES | VERIFICACIÓN | TIEMPOS

Seguir la ruta marcada del cable en rojo a lo largo de las tachuelas; DESCRIPCIÓN

#OP | IMAGEN | COMPONENTES | HERRAMIENTAS | ÚTILES | VERIFICACIÓN | TIEMPOS

Z | Seguir la ruta marcada del cable en rojo a lo largo de las tachuelas
Cable plano 15 vias | Recomendable fijar los cables con cinta de pintor.

#OP | IMAGEN | COMPONENTES | DESCRIPCIÓN | HERRAMIENTAS | ÚTILES | VERIFICACIÓN | TIEMPOS

| | H1


70 | t70


Seguir la ruta marcada del cable en rojo a lo largo de las
tachuelas

Seguir la ruta marcada del cable en rojo a lo largo de las
tachuelas

Cable plano de 20
vías

DESCRIPCIÓN; Cable plano 15 vías; Seguir la ruta marcada del cable en rojo a lo largo de las tachuelas

#OP | IMAGEN | COMPONENTES | HERRAMIENTAS | ÚTILES | VERIFICACIÓN | TIEMPOS

DESCRIPCIÓN; 2x DIN934 M3; llave de tubo 5,5mm; 1x Curve Flat Cable Holder; Apretar el Curve Flat Cable Holder aprisionando los dos cables planos; Desllizar el cable, haciéndolo pasar por debajo de las piezas de plástico. Collar fuerte las tuercas para fijar posición

#OP | IMAGEN | COMPONENTES | HERRAMIENTAS | ÚTILES | VERIFICACIÓN | TIEMPOS

Seguir la ruta marcada del cable en rojo a lo largo de las tachuelas; Cable plano 15 vías

#OP | IMAGEN | COMPONENTES | DESCRIPCIÓN | HERRAMIENTAS | ÚTILES | VERIFICACIÓN | TIEMPOS

#OP | IMAGEN | COMPONENTES | HERRAMIENTAS | ÚTILES | VERIFICACIÓN | TIEMPOS


100 | t100

DESCRIPCIÓN


110 | - | - | t110

E1 | Seguir la ruta marcada del cable en rojo a lo largo de las tachuelas
Cable plano 15 vías | Recomendable fijar los cables con cinta de pintor.

Posición final orientativa del cable

#OP | IMAGEN | COMPONENTES | HERRAMIENTAS | ÚTILES | VERIFICACIÓN | TIEMPOS


110 | t110

DESCRIPCIÓN


120 | Fijar los cables con cinta de pintor.

Seguir la ruta marcada del cable en rojo a lo largo de las
tachuelas

t120

Conectar el cable del SD Module en el orden mostrado en la imagen; DESCRIPCIÓN; Pasar el cable por la ruta y la tachuela mostradas en la imagen y dejar el extremo sin conectar; 1x SD Cable

#OP | IMAGEN | COMPONENTES | HERRAMIENTAS | ÚTILES | VERIFICACIÓN | TIEMPOS

DESCRIPCIÓN; 1x LCD Cable; Pasar el cable por la ruta y la tatxuela mostradas en la imagen y dejar el extremo sin conectar; Conectar el cable de la LCD del orden mostrado en la imagen, rojo a la izquierda; El cable blanco no está conectado

#OP | IMAGEN | COMPONENTES | HERRAMIENTAS | ÚTILES | VERIFICACIÓN | TIEMPOS

1x Power DC; Conectar los cables en el orden que se indica en la imagen en la fuente de alimentación que se encuentra a la derecha; Asegurarse de conectar en el orden adecuado; Destornillador de; estrella

#OP | IMAGEN | COMPONENTES | DESCRIPCIÓN | HERRAMIENTAS | ÚTILES | VERIFICACIÓN | TIEMPOS

Introducir el enchufe con los cables ya conectados y collar a la estructura con los tornillos avellanados. Si por defectos de fabricación no entrara en el agujero limar las paredes laterales.; 1x Power AC Cable; 1x Power Plug; Con la ayuda de los alicates, conectar las hembras a las lengüetas del enchufe en el orden determinado en la imagen (Amarillo / Verde - Tierra; Negro - linea; Azul - neutro); DESCRIPCIÓN; 2x DIN7991 M3x8; Llave allen 2mm; Alicates; Verficar conexionado según orden establecido y según los colores

#OP | IMAGEN | COMPONENTES | HERRAMIENTAS | ÚTILES | VERIFICACIÓN | TIEMPOS

#OP | IMAGEN | COMPONENTES | DESCRIPCIÓN | HERRAMIENTAS | ÚTILES | VERIFICACIÓN | TIEMPOS

1x Fuse

Introducir el fusible en el alojamiento del Power Plug. La orientación es indiferente.


Destornillador de
estrella Conectar los cables en el orden | - | t190
determinado en la imagen

t180

Asegurar el
orden de
connexión

Con la ayuda de los alicates, introducir los faston a las lengüetas del interruptor.; Introducir a presión el interruptor en el agujero lateral de la estructura; Asegurar que está el la orientación descrita en la imagen; 1x Power Button; Alicates

#OP | IMAGEN | COMPONENTES | DESCRIPCIÓN | HERRAMIENTAS | ÚTILES | VERIFICACIÓN | TIEMPOS

| | | Hacer pasar los extremos libres del cable a través del agujero lateral de la estructura

Asegurar el orden de connexión; 1x Power supply to Relay; Conectar el cable en el lugar determinado en la imagen. El cable rojo tiene que ir conectado en el canal 2 del Relay; Destornillador de; estrella

#OP | IMAGEN | COMPONENTES | DESCRIPCIÓN | HERRAMIENTAS | ÚTILES | VERIFICACIÓN | TIEMPOS

Colocar el USB a la estructura; 1x USB Extension Cable; Dejar el extremo libre; 2x DIN912 M3x10; DESCRIPCIÓ

#OP | IMATGE | COMPONENTS | EINES | ÚTILS | VERIFICACIÓ | TEMPS

Asegurar el orden de connexión; destornillador de; estrella; DESCRIPCIÓN; 1x Relay to Mainboard; Conectar al relay el cable que sale del relay a la main board. Canal 3 cable rojo (+) y canal 4 cable negro(-)

#OP | IMAGEN | COMPONENTES | HERRAMIENTAS | ÚTILES | VERIFICACIÓN | TIEMPOS

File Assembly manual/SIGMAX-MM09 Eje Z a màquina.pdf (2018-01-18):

## MANUAL DE MONTAJE

Colocar fuerte los Shaft Support inferiores a la estructura; CONJUNTO; Eje Z a máquina; Roscar del Z motor a traves del Husillo; Introducir las barras en los rodamientos lineales; 2x Z bar; 1x Z Axis structure; 4x DIN934 M5; Z motor; Tornillos de Shaft Support están orientados hacia el exterior; Llave de tubo 8mm

CODIGO DOCUMENTO | SIGMAX-MM09 | OPERARIOS | 1 | FECHA DOCUMENTO | 16/01/2018
VERSIÓN DOCUMENTO | v01 | TIEMPOS | T | CONTACTO | M.UCERO
#OP | IMAGEN | COMPONENTES | DESCRIPCIÓN | HERRAMIENTAS | ÚTILES | VERIFICACIÓN | TIEMPOS

Colocar y apretar fuerte los Shaft Support superiores a la estructura; Posicionar sin apretar las tuercas de los Shaft Support superiores; Colocar las barras con la z structure en los shaft support sujetandolas para que no se salgan de los rodamientos lineales; Llave de tubo 8mm; Tornillos de Shaft Support están orientados hacia el exterior; Z-structure; 4x DIN934 M5

#OP | IMAGEN | COMPONENTES | DESCRIPCIÓN | HERRAMIENTAS | ÚTILES | VERIFICACIÓN | TIEMPOS

Unir el conector hembra del hot bed cable con el macho que conecta a la mainboard; Apretar los tornillos de los shaft support para que las barras queden bien fijadas; Llave allen; llave de tubo 5,5mm; Colocar el z motor support a la estructura y apretar fuerte las tuercas DIN 1587 M3; Tornillos de Shaft Support están orientados hacia el exterior; Instalar el terminal con forma de horquilla que contiene los cables rojos y atornillar en el canal 1 del relay; Destornillador de; estrella; Verificar que el cable rojo de hot bed esta en el canal 1 del Relay; 2x DIN1587 M3

#OP | IMAGEN | COMPONENTES | DESCRIPCIÓN | HERRAMIENTAS | ÚTILES | VERIFICACIÓN | TIEMPOS

verificar la correcta conexión en el terminal negativo de la fuente de alimentación; Instalar los terminales con forma de horquilla de los cables negros y atornillar en los terminales negativos de la fuente de alimentación; Destornillador de estrella; 1x Hot bed cable clip; 2X DIN934 M3; Pasar el hot bed cable a traves del clip y apretar las tuercas; Llave de tubo de 5,5mm

#OP | IMAGEN | COMPONENTES | DESCRIPCIÓN | HERRAMIENTAS | ÚTILES | VERIFICACIÓN | TIEMPOS

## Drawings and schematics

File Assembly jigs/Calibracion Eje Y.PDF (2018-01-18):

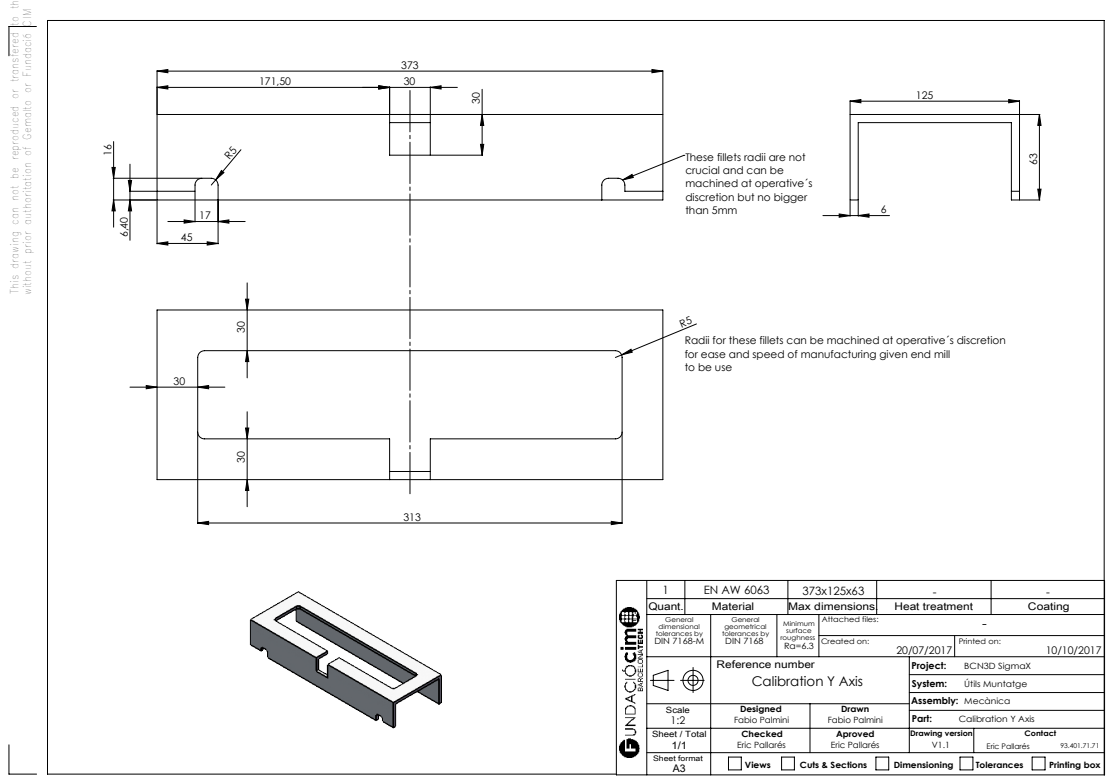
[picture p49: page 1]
Max dimensions.; Heat treatment; Coating; Created on:; Printed on:; Views; Cuts & Sections; Dimensioning; Tolerances; Printing box; Calibration Y Axis

This drawing can not be reproduced or transfered to third parts

without prior authoritation of Gemalto or Fundació CIM

These fillets radii are not
crucial and can be
machined at operative´s
discretion but no bigger
than 5mm

Radii for these fillets can be machined at operative´s discretion
for ease and speed of manufacturing given end mill
to be use

General dimensional tolerances by DIN 7168-M | General geometrical tolerances by DIN 7168 | Minimum surface roughness Ra=6.3 | Attached files: | -

Reference number Calibration Y Axis | Project: BCN3D SigmaX System: Útils Muntatge Assembly: Mecànica

Scale 1:2 | Designed Fabio Palmini | Drawn Fabio Palmini

Sheet / Total 1/1 | Checked Eric Pallarés | Aproved Eric Pallarés | Drawing version V1.1 | Contact Eric Pallarés 93.401.71.71

Sheet format A3
